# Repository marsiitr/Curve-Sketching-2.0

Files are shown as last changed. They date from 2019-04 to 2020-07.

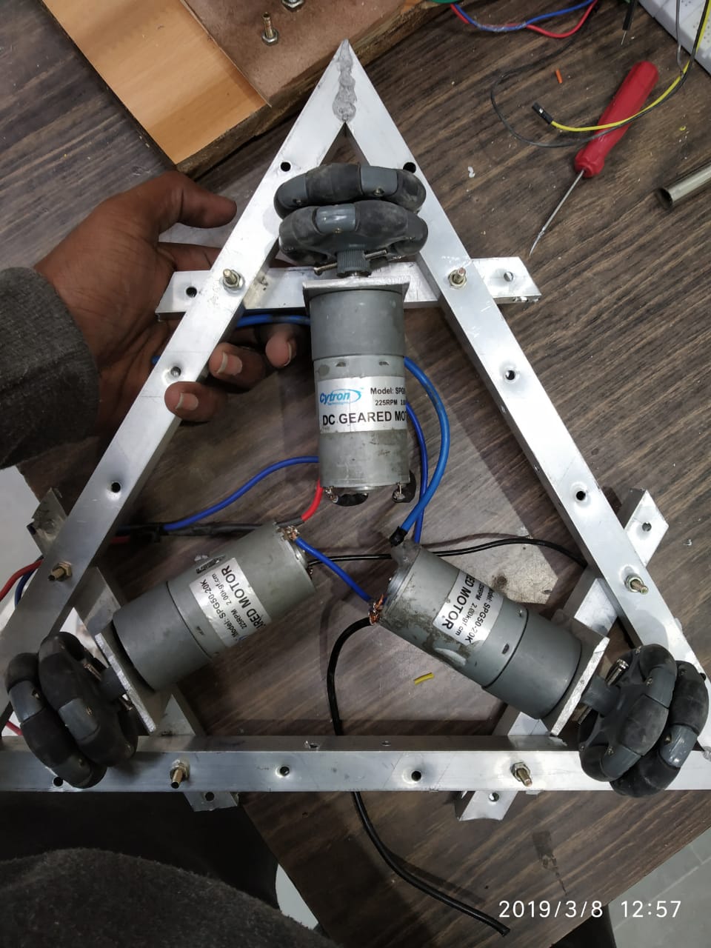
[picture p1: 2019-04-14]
Images and Videos/Images/Mechanical Structure.jpeg

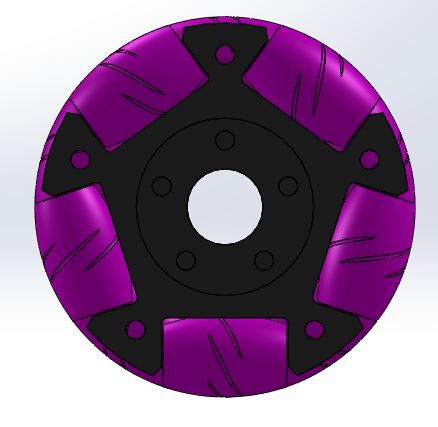
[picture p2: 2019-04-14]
Mechanical Design/nx54141-60mm-aluminum-double-omni-wheel-1.snapshot.1/002.JPG

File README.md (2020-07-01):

# Curve Sketching Bot 2.0
### Srishti 2019

## Abstract

The aim of this project was to make a bot that can sketch any given curve on a plane surface. 

 Curve

## Motivation

There is no handy product in the market to sketch or plot curves on large scale canvas.

The previous version of this bot-Curve Sketching Bot (Srishti 2018) traverses using differential chassis. It was disadvantageous since it was slow and had to change its orientation every time to move along the curve.

Hence we came up with the idea of making an advanced version of the bot that is faster, moves in a locked orientation, and with other possible advanced features.

## Materials Required

* 5x 58mm plastic omni-wheel.
* 3x 300rpm DC motors.
* 2x Rotary Encoders.
* 1x Arduino Mega.
* 2x Cytron motor drivers.
* 1x Gyroscope(MPU 9250).
* 1X 5V Regulator(7805).
* 1x 9V Regulator(7809).
* 2x Linear Bearings.
* 2x switches.
* 3d printed parts.
* 1x Full Bread board.
* Jumper wires.
* Aluminium square channels+plates.
* 1x 11.1V 2200mAh LiPo battery.
* 1x Pen.
* 1x Spring.

## Mechanical Aspect Of Design

### Chassis
It is an equilateral triangle-shaped, 3 wheeled Omni drive bot that can be easily manufactured. Omni drives are really fast, it can move in any direction without changing its orientation i.e., in locked orientation and the wheels always stay in contact with the ground even if the surface is uneven.

### Material
The chassis is made up of square aluminum channels. It reduces the overall weight of the bot and hence reducing the load on motors.

### Motor Assembly
Three Johnson 300rpm motors are used, to get the required torque. They are coupled with Omni wheels using 3D printed couplers and the shaft of the motor is passed through radial ball bearing. The bearing block is mounted on the chassis holding the wheel assembly and chassis together. The three wheel assemblies are mounted on the three vertices of the triangular chassis i.e., at 120° to each other.

### Encoder Assembly
Two encoders are mounted mutually perpendicular to each other on the triangular chassis with their axes intersecting at the centroid of the chassis. And two free wheels are attached to these encoders to get feedback from the 'x' and 'y' axes. This encoder assembly is mounted on the chassis using a hinge so that all five wheels can have proper contact with the surface.

### Pen Holder
It is a 3D printed cylindrical holder that is placed at the centroid of the chassis. It can hold only one pen at a time and the size of the holder is fixed and hence the pen diameter is fixed. 

### Electronic Components
All electronic components are placed on the top of the chassis with cardboard as the base to reduce weight and to avoid short circuits as aluminum is an electric conductor.

## Electronics Aspect Of Design

### Code Algorithm
1. All actuations are done with appropriate velocities which are calculated by dividing the curve into small distances.
2. Feedbacks are obtained from encoders and MPU9250.
3. PID mechanism is the control loop mechanism here. It changes the velocities according to the obtained feedback.
4. This process is done in a loop until the curve is fully plotted.

### Microcontroller
Arduino Mega 2560 R3 is used as the microcontroller board.

### Sensors
* MPU9250 is used to get the angular motion feedback of the bot. It is directly connected to SDA/SCL sockets of the Arduino Mega board through male headers as wires interrupt serial communication.
* Two Rotary Encoders are used to get linear motion feedback from x and y axes.

### Actuators
* Jhonson 300rpm motors are used for traversal actuation which is controlled by Cytron motor driver.

### Other Components
* IC LM7809 and IC LM7805 for converting 11.1V DC to 9V DC and 5V DC respectively
* Two switches are used-One for motor drivers and another for the rest of the bot. 

### Power Source
* 11.1V LiPo battery is used as the power source.
* Motors are directly powered from the battery.
* Arduino Mega board is powered with 9V converted output of the battery.
* Encoders are powered with 5V converted output of the battery.
* MPU9250 is powered with 5V Vcc of Arduino.

## Cost Structure 

|Components|Cost(INR)|
|---|---|
|Wheels|5*450|
|Linear Bearing|2*100|
|Gyroscope(MPU 9250)|1*450|
|Motors|3*500|
|Motor Drive|2*2500|
|Arduino Mega|1*650|
|Bread Board|1*100|
|11.1V LiPo Battery|1*750|
|Aluminium square channels|1*100|
|**Total**|**11,000**|
## Applications

It can be used to plot any continuous curve on plane canvas of any scale.

## Limitations

* It cannot be used to plot discontinuous curves.
* The pen size is fixed.
* It can plot only in one color. 

## Future Improvements

* A servo motor can be attached to the pen holder to make it possible for the bot to plot discontinuous curves.
* Pen holder design can be changed to hold multiple pens to make the bot plot in multiple colors.
* The code can be improved to plot images using G-code.

## Team Members
1.  Ruchika Atul Guntewar
2.  Sanjeev Krishnan R.
3.  Vijai Kumar R.

## Mentors

1.  Ujjwal Baranwal
2.  Vedant Neekhra
Team
## References
 
<https://www.google.com/amp/s/amp.livescience.com/40103-accelerometer-vs-gyroscope.html>

<https://www.autonomousrobotslab.com/pid-control.html>

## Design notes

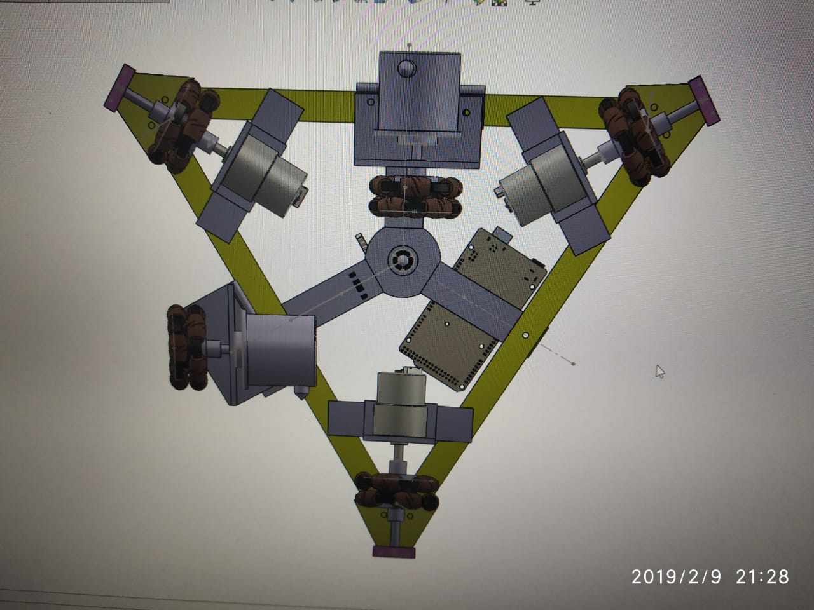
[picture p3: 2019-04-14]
Mechanical Design/bot bottom view 1.jpeg

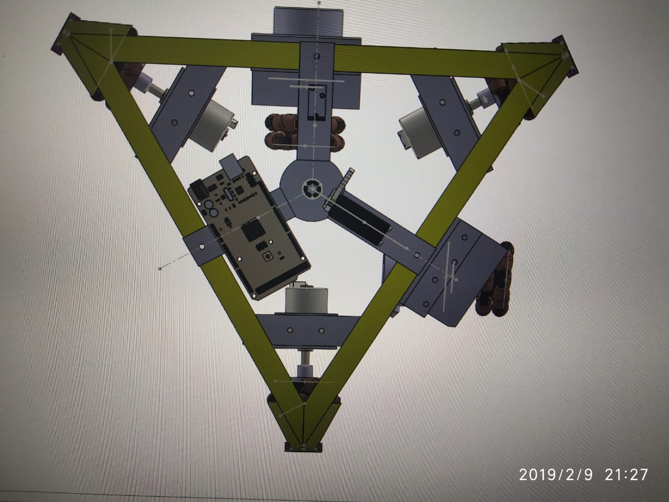
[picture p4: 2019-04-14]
Mechanical Design/bot top view.jpeg

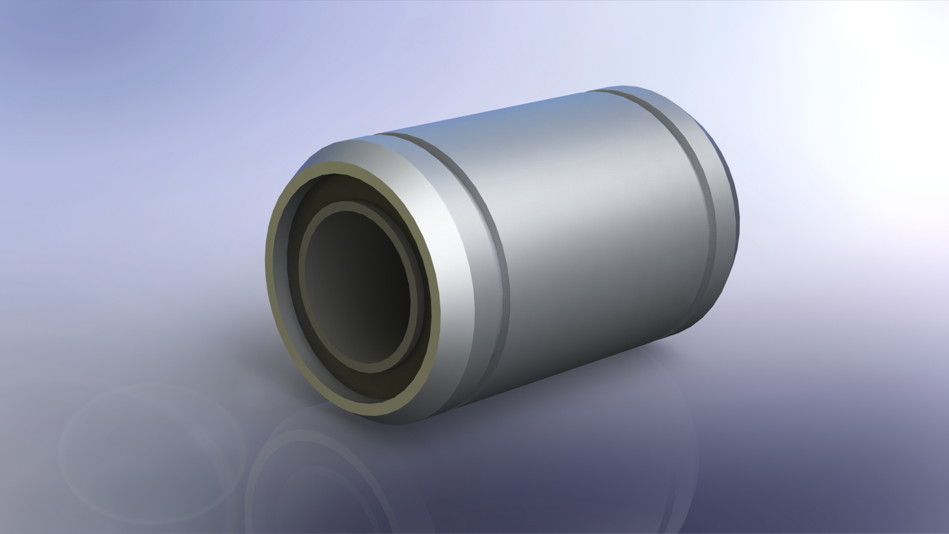
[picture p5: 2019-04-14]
Mechanical Design/lm8uu-linear-ball-bearing-1.snapshot.1/lm8uu.JPG

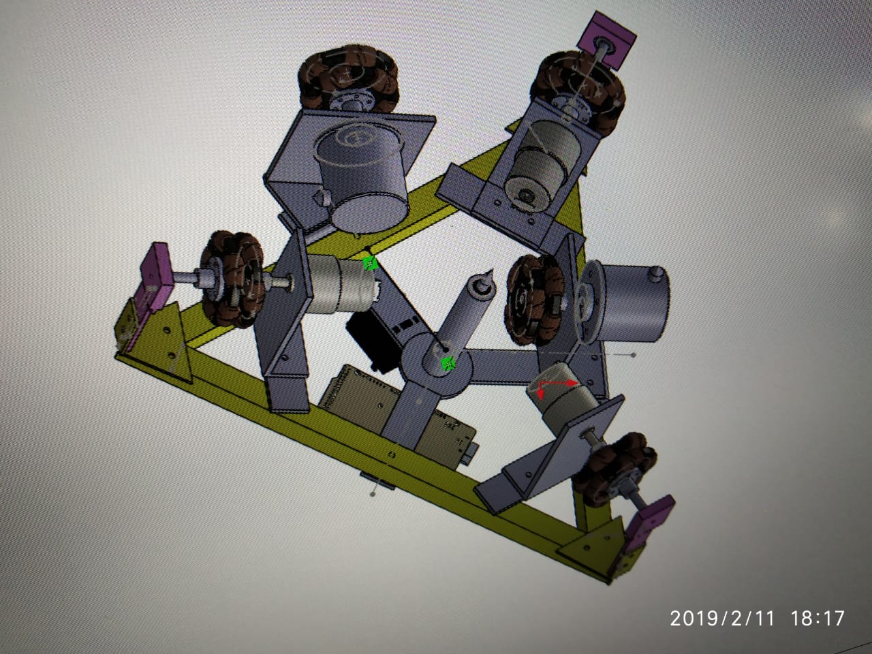
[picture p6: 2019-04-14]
Mechanical Design/bot view.jpeg

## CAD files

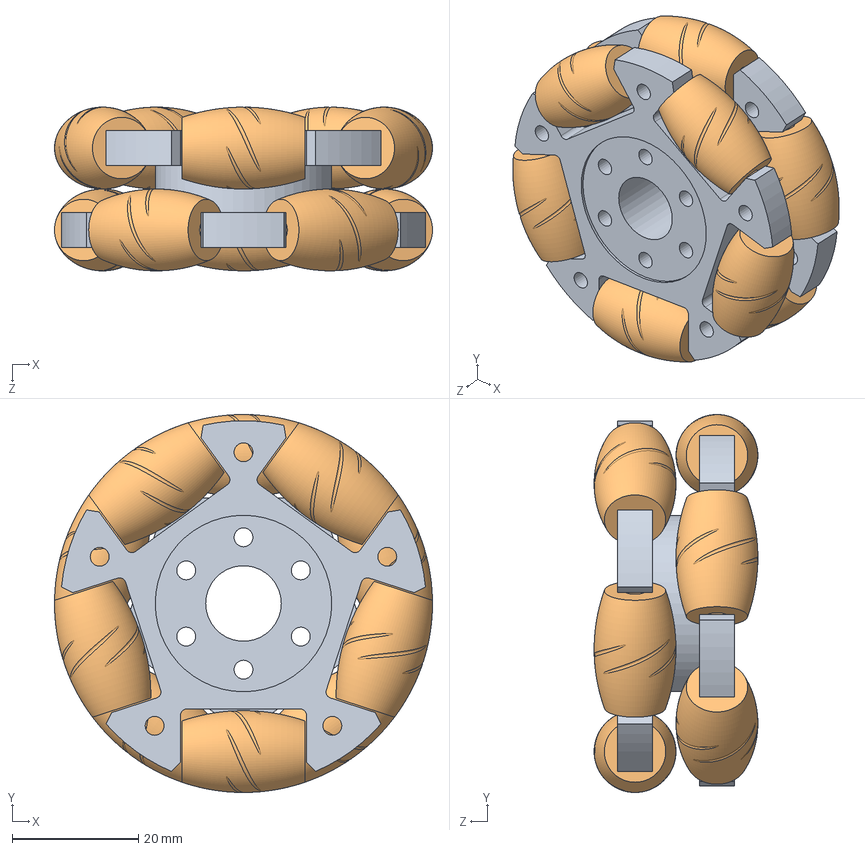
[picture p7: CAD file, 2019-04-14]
Mechanical Design/nx54141-60mm-aluminum-double-omni-wheel-1.snapshot.1/OMNI WHEEL.SLDASM
60.0 x 60.0 x 26.0 mm
Part1^OMNI WHEEL
Part2^OMNI WHEEL x 10

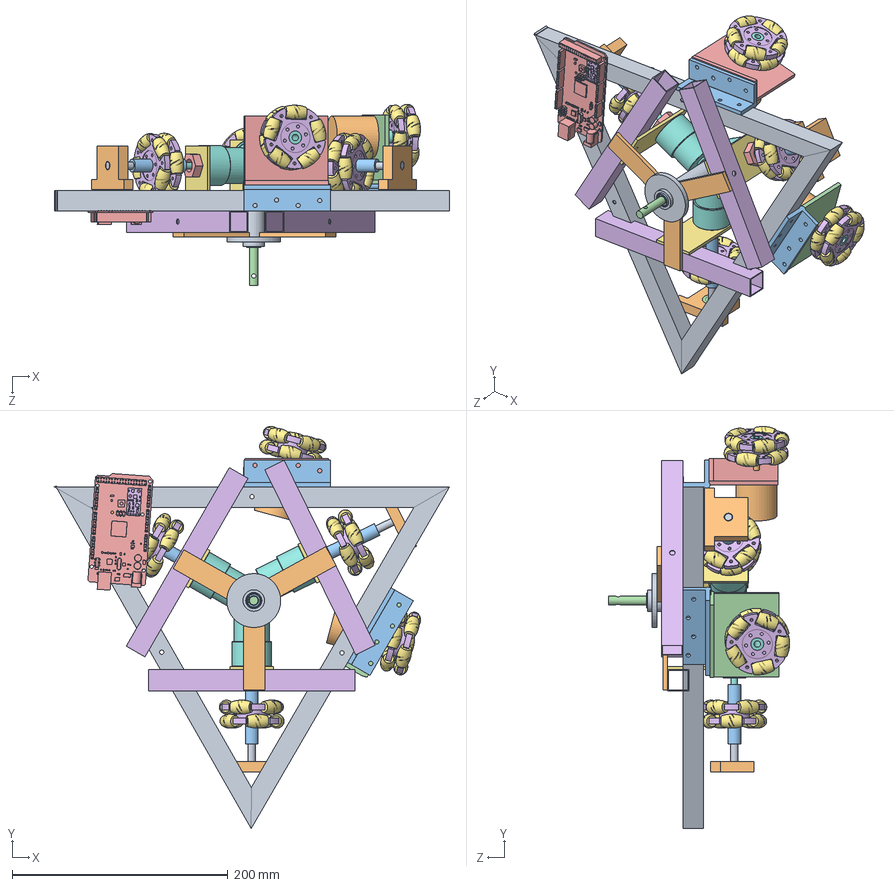
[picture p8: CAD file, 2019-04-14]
Mechanical Design/final design of bot.SLDASM
366.0 x 372.6 x 168.1 mm
chasis frame sides x 3
OMRON E6CP-AG5C-C x 2
hinge x 2
encoder support plate 1
encoder support plate 2
new motor support x 3
new motor support plate x 3
DC motor x 3
shaft x 3
wheel joint revised x 3
new wheel mount x 3
bearing x 3
new motor screw x 3
Part1^OMNI WHEEL x 5
Part2^OMNI WHEEL x 50
new encoder wheel mount x 2
circle
circle frame joint x 3
lm8uu x 2
pen
ArduinoMega
Pol

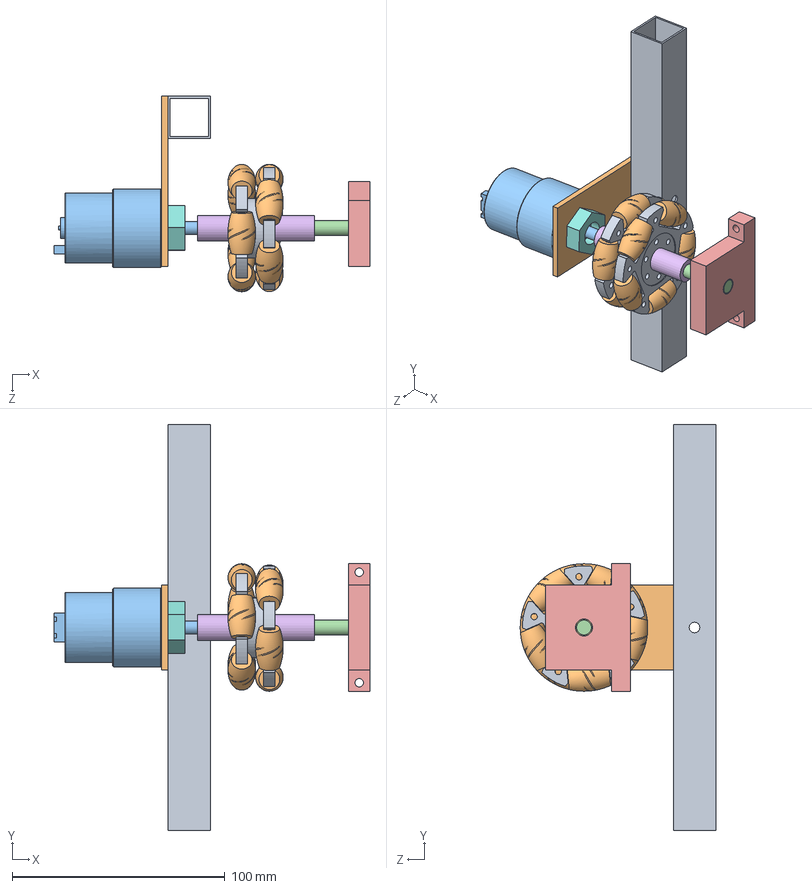
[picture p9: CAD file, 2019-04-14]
Mechanical Design/whole wheel setup.SLDASM
148.5 x 191.0 x 92.0 mm
new motor support
new motor support plate
DC motor
shaft
wheel joint revised
new wheel mount
bearing
new motor screw
Part1^OMNI WHEEL
Part2^OMNI WHEEL x 10

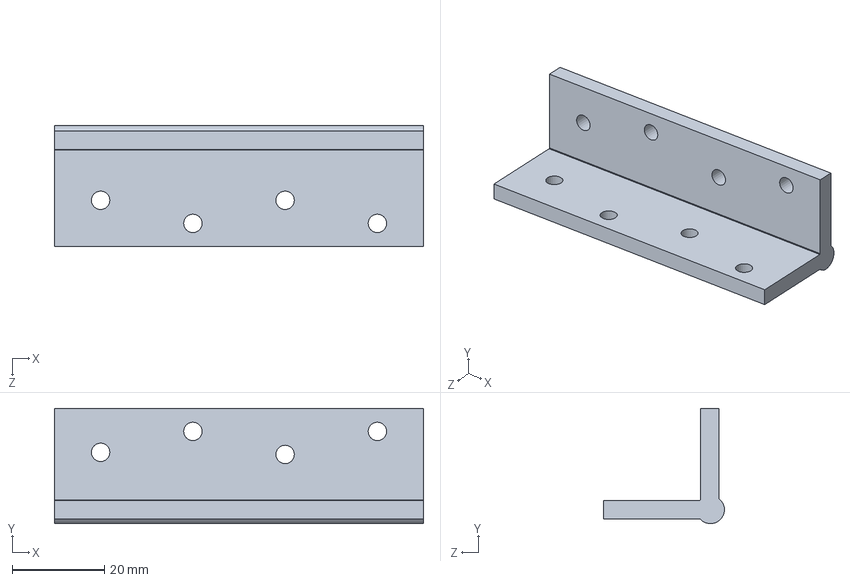
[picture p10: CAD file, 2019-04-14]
Mechanical Design/hinge.SLDPRT
80.0 x 25.0 x 26.2 mm

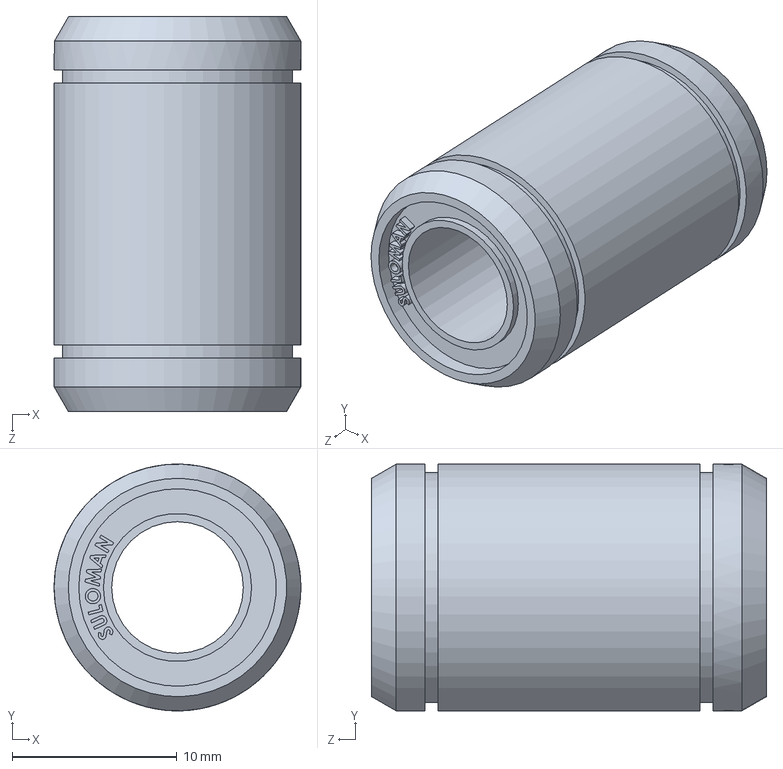
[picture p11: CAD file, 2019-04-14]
Mechanical Design/lm8uu-linear-ball-bearing-1.snapshot.1/lm8uu.SLDPRT
15.0 x 15.0 x 24.0 mm

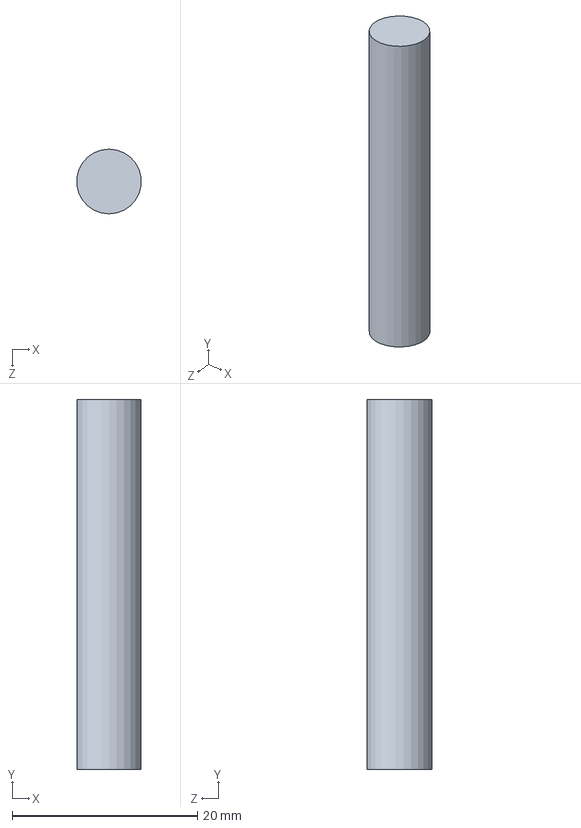
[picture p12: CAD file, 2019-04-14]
Mechanical Design/wheel support shaft.SLDPRT
6.95 x 40.0 x 7.00 mm

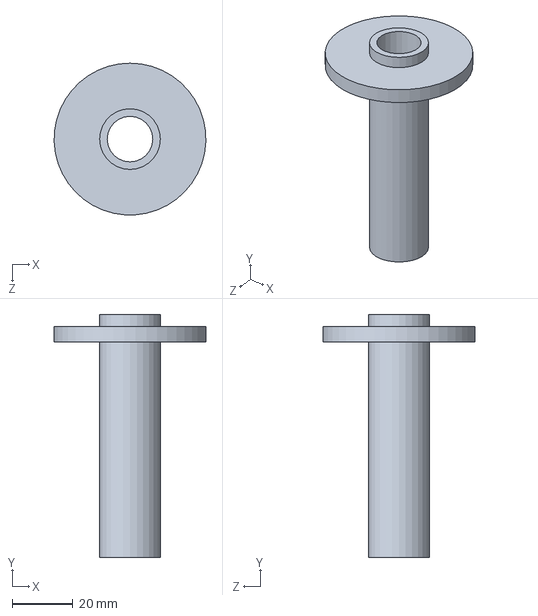
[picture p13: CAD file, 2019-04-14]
Mechanical Design/pen holder.SLDPRT
50.0 x 80.0 x 49.9 mm

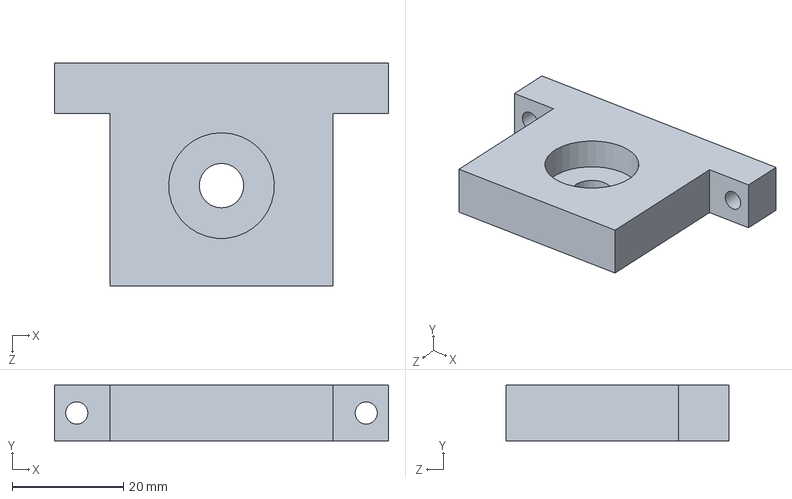
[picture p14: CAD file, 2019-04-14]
Mechanical Design/wheel support mount.SLDPRT
60.0 x 10.0 x 40.0 mm

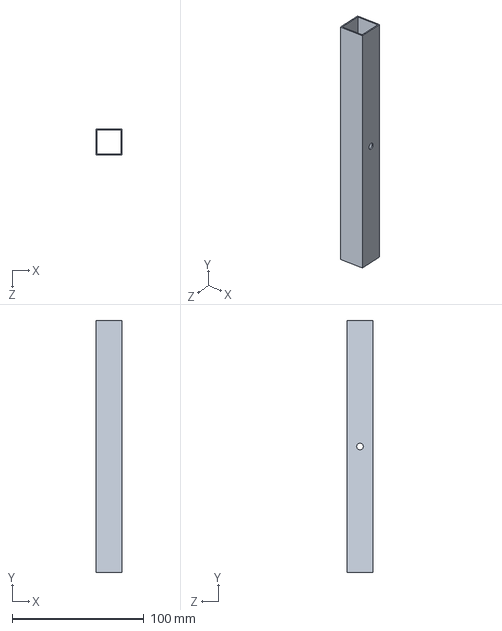
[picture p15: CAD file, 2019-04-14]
Mechanical Design/joint to motor mount.SLDPRT
20.0 x 191.0 x 20.0 mm

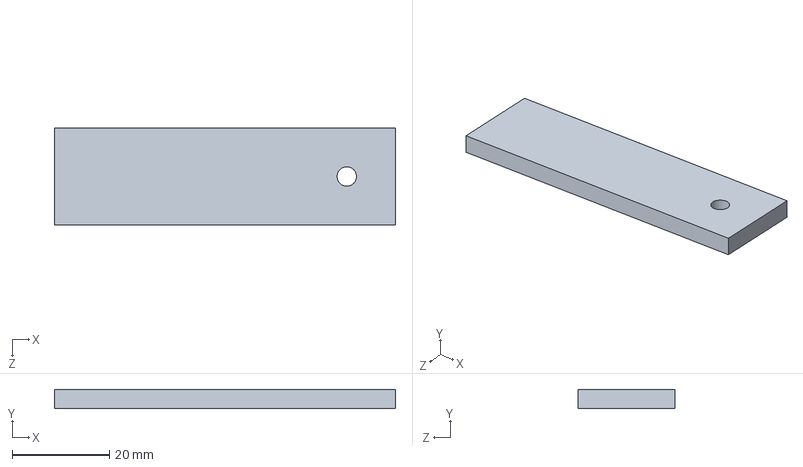
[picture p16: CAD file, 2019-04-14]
Mechanical Design/pen holder support.SLDPRT
70.0 x 4.00 x 20.0 mm

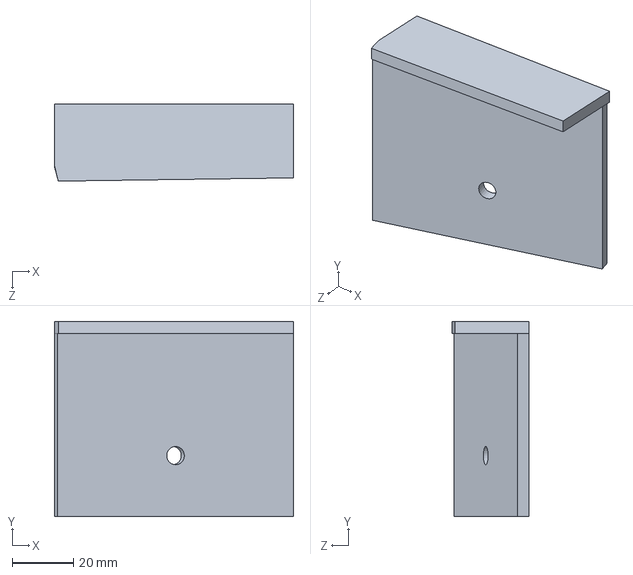
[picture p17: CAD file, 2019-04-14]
Mechanical Design/encoder support plate 1.SLDPRT
78.3 x 64.0 x 25.3 mm

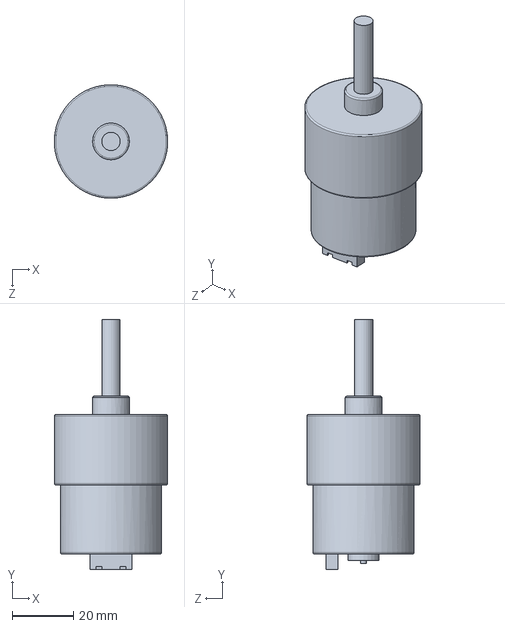
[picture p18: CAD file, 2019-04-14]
Mechanical Design/DC motor.SLDPRT
37.0 x 81.5 x 37.0 mm

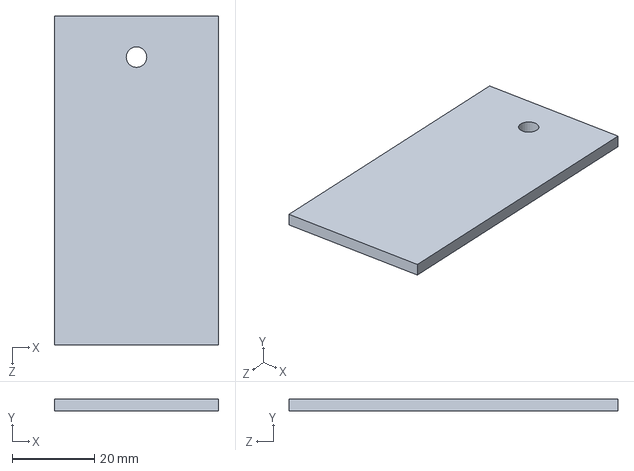
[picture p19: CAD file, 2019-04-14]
Mechanical Design/motor support plate.SLDPRT
40.0 x 3.00 x 80.0 mm

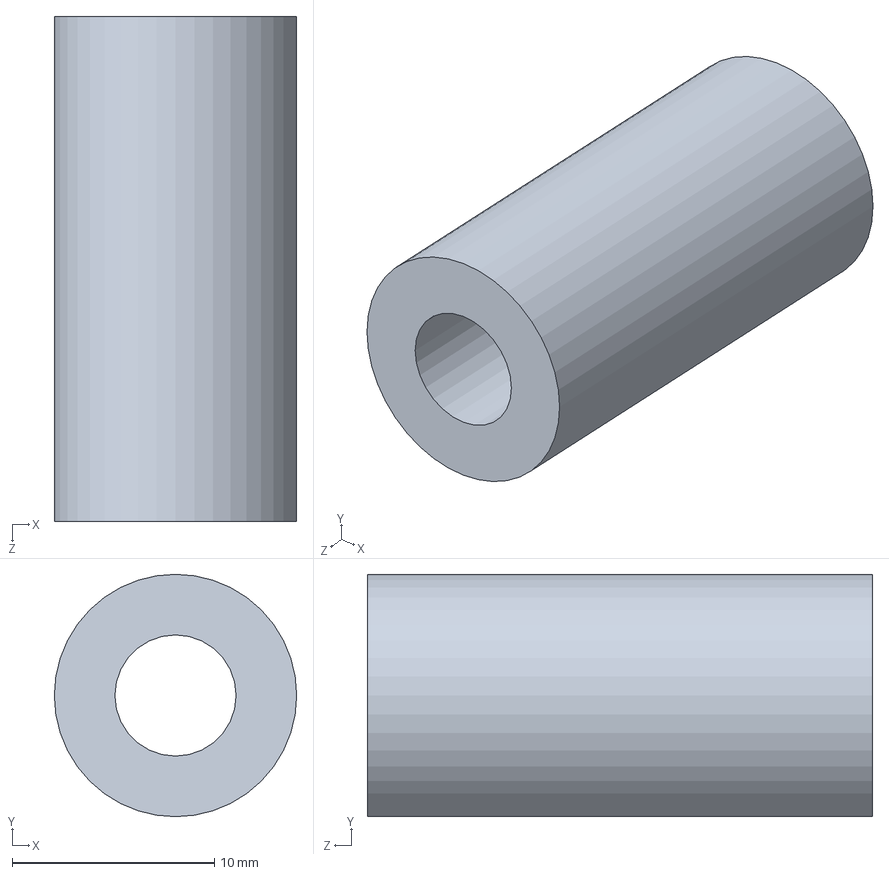
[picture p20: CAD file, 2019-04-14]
Mechanical Design/encoder wheel mount.SLDPRT
12.0 x 12.0 x 25.0 mm

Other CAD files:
Mechanical Design/OMNI WHEEL.SLDASM
Mechanical Design/lm8uu.SLDPRT
Mechanical Design/ArduinoMega.SLDPRT
Mechanical Design/pen.SLDPRT
Mechanical Design/chasis frame sides.SLDPRT
Mechanical Design/encoder support plate 2.SLDPRT
Mechanical Design/motor screw.SLDPRT
Mechanical Design/mpu(gyro).SLDPRT
Mechanical Design/wheel coupling.SLDPRT

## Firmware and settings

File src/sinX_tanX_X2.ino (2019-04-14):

#include <MPU9250.h>
const double pi = 3.1415926535897932384626433832795;
int v[3] = {0, 0, 0}, V = 100, motPin[3] = {8, 9, 10}, motAnalog[3] = {11, 12, 7}, encPin[4] = {33, 2, 35, 3};
volatile int counterx = 0, countery = 0;
float ang = 0, ax = 0, ay = 0, cx = -15, cy = 0, tx = 0, ty = 0, actEe, actEy, actEg, Kp1 = 0.5, Kp2 = 4, Kd1 = 0, Kd2 = 0, w1 = 0, g1 = 0, w;//3.15

MPU9250 IMU;

double t;

int16_t gyro[3] = {0, 0, 0};
int16_t acc[3] = {0, 0, 0};
float gyroBias[3]  = {0, 0, 0};
float accelBias[3] = {0, 0, 0};
int dt;
long Time;
double ix = -15.0 , iy = 0.0;

double x = 0.0, y = 0.0;
double cosine , sine;
double offset;
double gyr_angle = 0.00;
double sum = 0;

void read_gyro() {
  if ((micros() - Time) > 13000) {
    IMU.readGyroData(gyro);
    dt = micros() - Time;
    gyr_angle += (gyro[2] - gyroBias[2]) * dt / 131.0 / 1000000.0;
    Time = micros();
  }
}

float rad(float a)
{
  return a * 2 * pi / 360;
}
float f(float x) //this code can plot 3 curves by changing pins in arduino...to plot some other curve change the returning function accordingly.
{
 if(digitalRead(37)==HIGH)
  return 15 * sin(0.1 * x); //0.1 * x * x;
 else if(digitalRead(39)==HIGH)
  return 0.08*x*x;
 else
  return 15*atan(0.1*x);
}
void basev(float a, float b, float c, float d)
{
  ang = atan((d - b) / (c - a));
}

void base_pwm() {
  v[0] = V * (cos(rad(0)) * cos(ang) + sin(rad(0)) * sin(ang));
  v[1] = V * (cos(rad(240)) * cos(ang) + sin(rad(240)) * sin(ang));
  v[2] = V * (cos(rad(120)) * cos(ang) + sin(rad(120)) * sin(ang));
}

void wheels()
{
  for (int i = 0; i < 3; i++)
  {
    
    analogWrite(motAnalog[i], constrain(abs(v[i]) , 0 , 255));
    
    if (v[i] >= 0)
    {
      digitalWrite(motPin[i], LOW);
      
    }
    else
    {
      
      digitalWrite(motPin[i], HIGH);
    }
  }
}
void enc_read()
{
  float disx = counterx * 5.8 * pi / 600.0;
  float disy = countery * 5.8 * pi / 600.0;
  cy = disy * cos(rad(gyr_angle)) - disx * sin(rad(gyr_angle));
  cx = disy * sin(rad(gyr_angle)) + disx * cos(rad(gyr_angle));
}


void setup() {
  Serial.begin(9600);
  pinMode(37,INPUT);

  for (int i = 0; i < 3; i++)
    pinMode(motPin[i], OUTPUT);
  for (int i = 0; i < 3; i++)
    pinMode(motAnalog[i], OUTPUT);
  for (int i = 0; i < 4; i++)
    pinMode(encPin[i], INPUT_PULLUP);
  attachInterrupt(digitalPinToInterrupt(encPin[1]), ai0, RISING);
  attachInterrupt(digitalPinToInterrupt(encPin[3]), ai1, RISING);


  for (int i = 0; i <= 10 ; i++) {
    IMU.readGyroData(gyro);
    sum += gyro[2];
    delay(10);
  }
  gyroBias[2] = sum / 11.0;
  ang = 0;
  
}

void loop() {
  
  if (cx >=tx) {
    ix = cx;
    iy = cy;
    tx = ix + 0.1 ;
    ty = f(tx);
    basev(ix, f(ix), tx, ty);
    
  }
  
  read_gyro();
  enc_read();
  w = cy - f(cx);
  actEe = w * Kp1 + (w - w1) * Kd1;
  w1 = w;
  actEg = gyr_angle * Kp2 + (gyr_angle - g1) * Kd2;
  g1 = gyr_angle;

  base_pwm();
  v[0] += actEg;
  v[1] += (actEg + actEe);
  v[2] += (actEg - actEe);

  wheels();
    Serial.println(gyr_angle);

  if(cx >= 65)
  {
    for (int i = 0; i < 3 ; i++)
    {
      v[i] = 0;
    }
    wheels();
    while(1);
  }


}



void ai0()
{
  if (digitalRead(encPin[0]) == LOW)
    counterx--;
  else
    counterx++;
}
void ai1()
{
  if (digitalRead(encPin[2]) == LOW)
    countery++;
  else
    countery--;
}
